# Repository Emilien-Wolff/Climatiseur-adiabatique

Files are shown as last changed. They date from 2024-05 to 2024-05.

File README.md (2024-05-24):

# Climatiseur adiabatique 🌊

> [!NOTE]
> Un projet réalisé dans le but de créer un climatiseur basé sur un principe simple : lorsque l'eau s'évapore, elle absorbe la chaleur environnante, et refroidit donc l'air

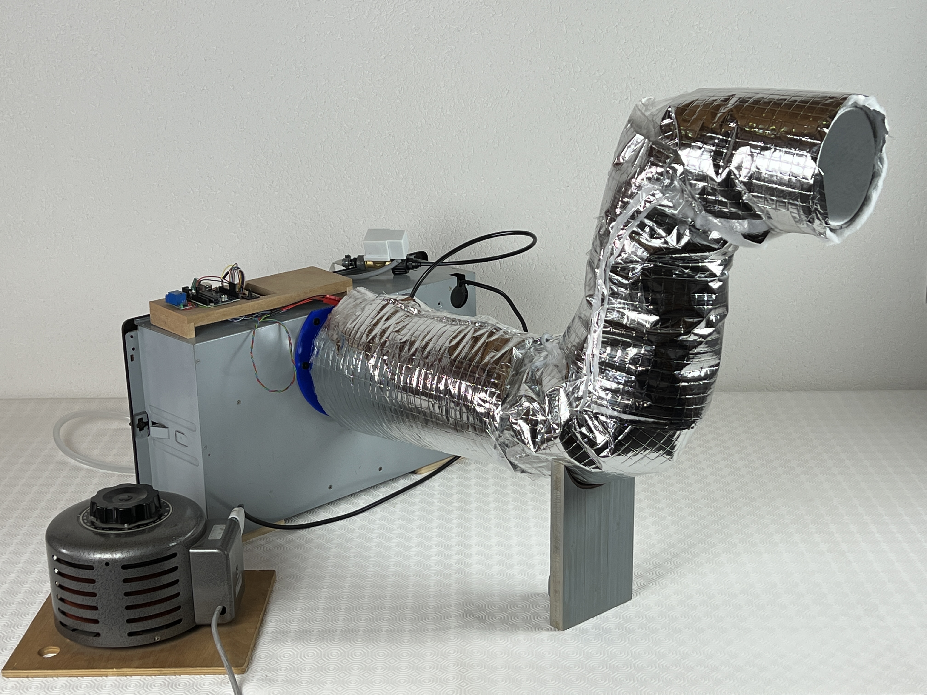
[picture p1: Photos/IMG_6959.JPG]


## Mon objectif

> Quantifier l'efficacité d'un tel système et proposer un système peu cher, compact et suffisament efficace pour permettre en été caniculaire de dormir correctement, sans travail mécanique $W_\text{méca}$ apporté (compresseur).

## Mon cahier des charges

 - Confort d'habitation en été
 - Disposer d'un système compact
 - Consommation faible d'eau et d'électricité
 - Bruit de fonctionnnement faible

## FAQ

#### Pourquoi ne pas prendre une clim classique ?

Les gaz utilisées dans les pompes à chaleur sont nocifs pour la planète, et le coût global de l'appareil est élevé pour des ménages à faibles revenus, qui de ce fait ne peuvent pas bénéficier d'une qualité de vie lors des étés chauds.

#### Risques de moisissures par l'humidité ?

Oui, j'y ai pensé, et propose des solutions à la fin de ma présentation

#### Y-a-t-il un produit final ?

Pour l'instant, non, j'ai effectué une maquette complète qui montre qu'on peut gagner environ 10°C, mais la surface d'échange devrait augmenter pour atteindre une puissance suffisante et refroidir un appartement. Projet en suspend ... Ca nécessiterait un travail sur la surface d'échange.

## 🚀 Qui suis-je ?
Je suis actuellement en deuxième année de classe préparatoire aux écoles d'ingénieur au lycée Kléber de Strasbourg

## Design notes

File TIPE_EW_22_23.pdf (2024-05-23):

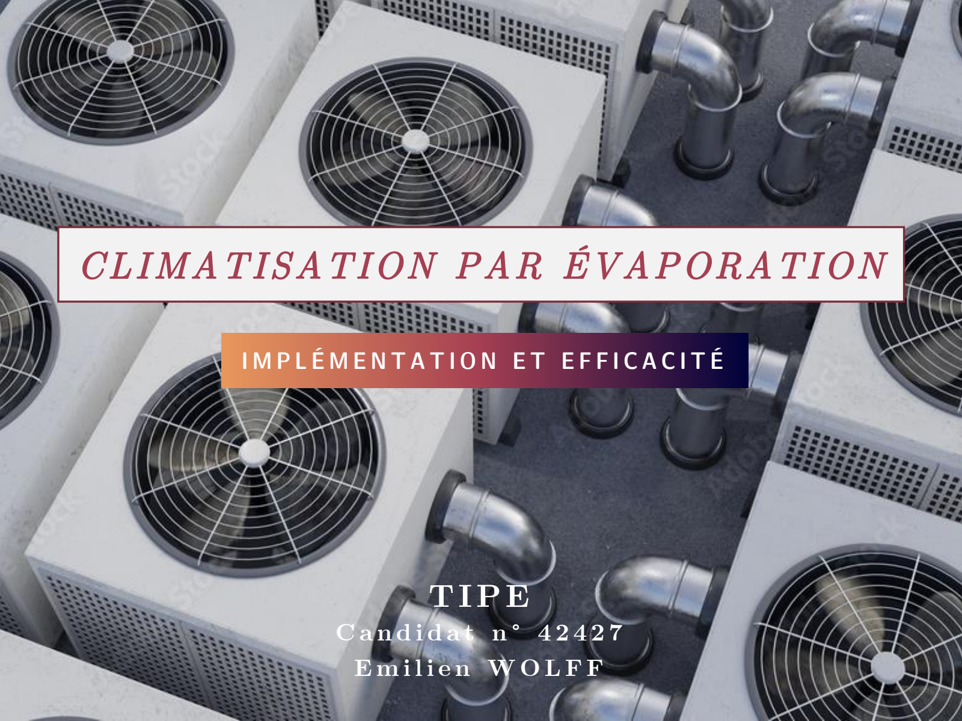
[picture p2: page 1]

# CL IMATISATION PAR ÉVAPORATION

# C a n d i d a t n ° 4 2 4 2 7

# I M P L É M E N T A T I O N E T E F F I C A C I T É

# T IPE

# E m i l i e n W O L F F

# SOMMAIRE

# 1 – Mi se e n c o nte x te e t C DC F

# 2 – Maq ue tte c o nc e ptue l l e

# 3 – Ré sul tats e t anal y se s

# 4 – C o nc l usi o n

P r o b l é m a t i q u e | : | p a r | q u e l s

# m o y e n s p e u t - on d i s p o s e r d ’ u n

s y s t è m e | de | c l i m a t i s a t i o n

# e f f i c a c e d ’ u n e p i è c e , c o m p a c t

# et p e u c o u t e u x ?

# 1 – MISE EN CONTEXTE ET CDCF

# H I S T O R I Q U E

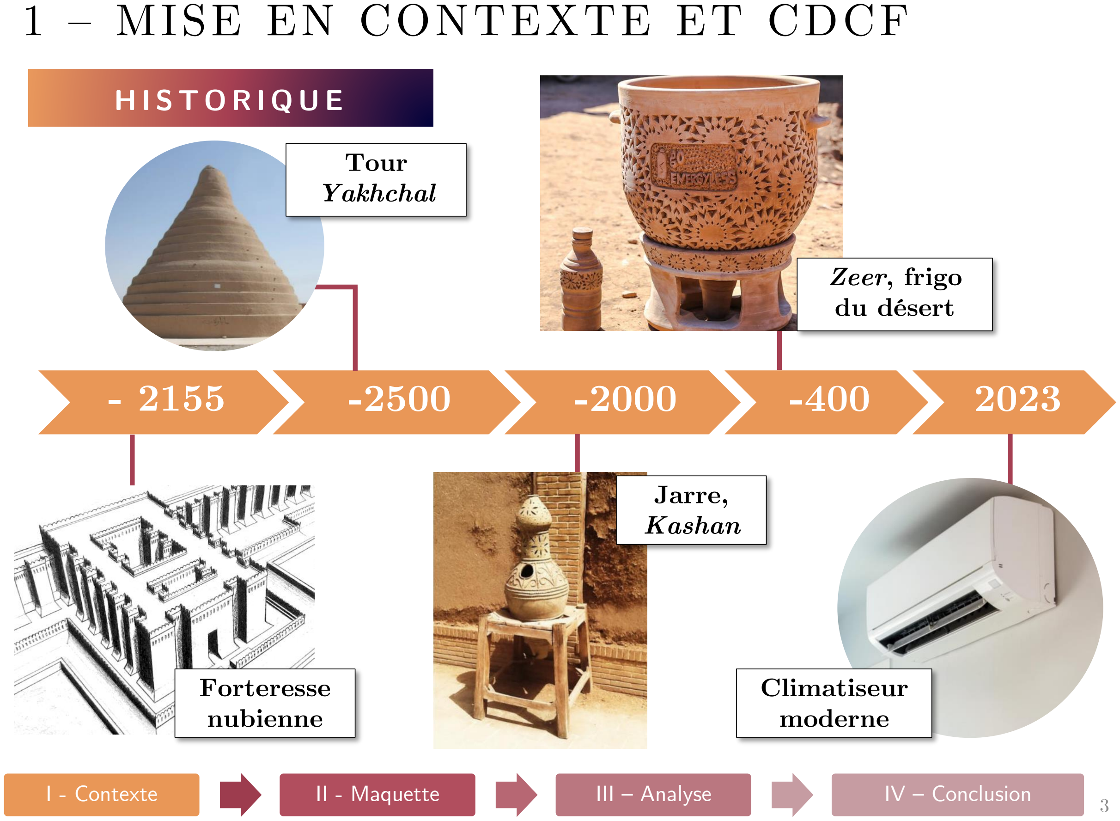
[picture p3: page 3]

- 2155 | -2500 | -2000 | -400 | 2023
I - Contexte | II - Maquette | III – Analyse | IV – Conclusion

# Forteresse nubienne

Jarre,

# Kashan

# Zeer, frigo du désert

# Climatiseur moderne

# Tour Yakhchal

# 1 – MISE EN CONTEXTE ET CDCF

# E X E M P L E

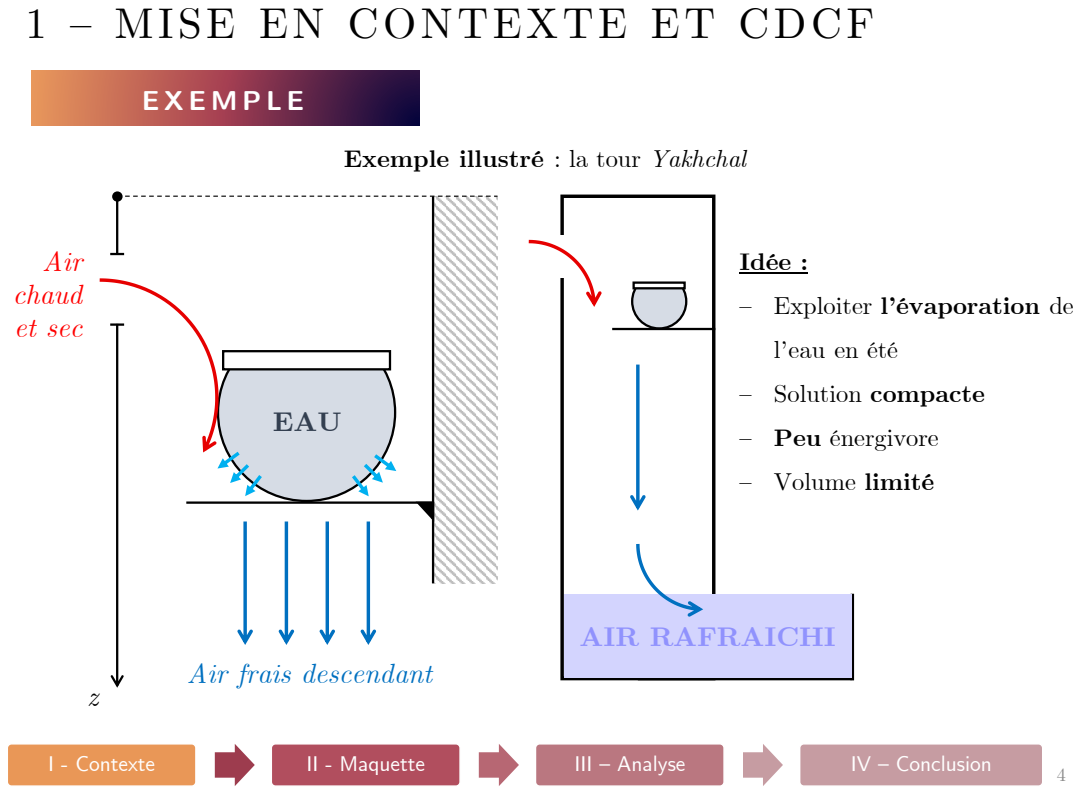
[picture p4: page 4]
Air chaud et sec; EAU; AIR RAFRAICHI

Exemple illustré : la tour Yakhchal

Idée :
– Exploiter l’évaporation de
l’eau en été
– Solution compacte
– Peu énergivore
– Volume limité

Air frais descendant

# 1 – MISE EN CONTEXTE ET CDCF

# P R I N C I P E S

18°C
20%

25°C
30%

35°C
30%

40°C
30%

## Pièce

## EXTERIEUR

# Figure 1 : Refroidissement par échangeur

28°C
30%

# – Cyclage interne de l’air

# – Compresseur, échangeurs, fluide

# – Assèchement de l’air interne

## Flux de chaleur entrant

# 1 – MISE EN CONTEXTE ET CDCF

# P R I N C I P E S

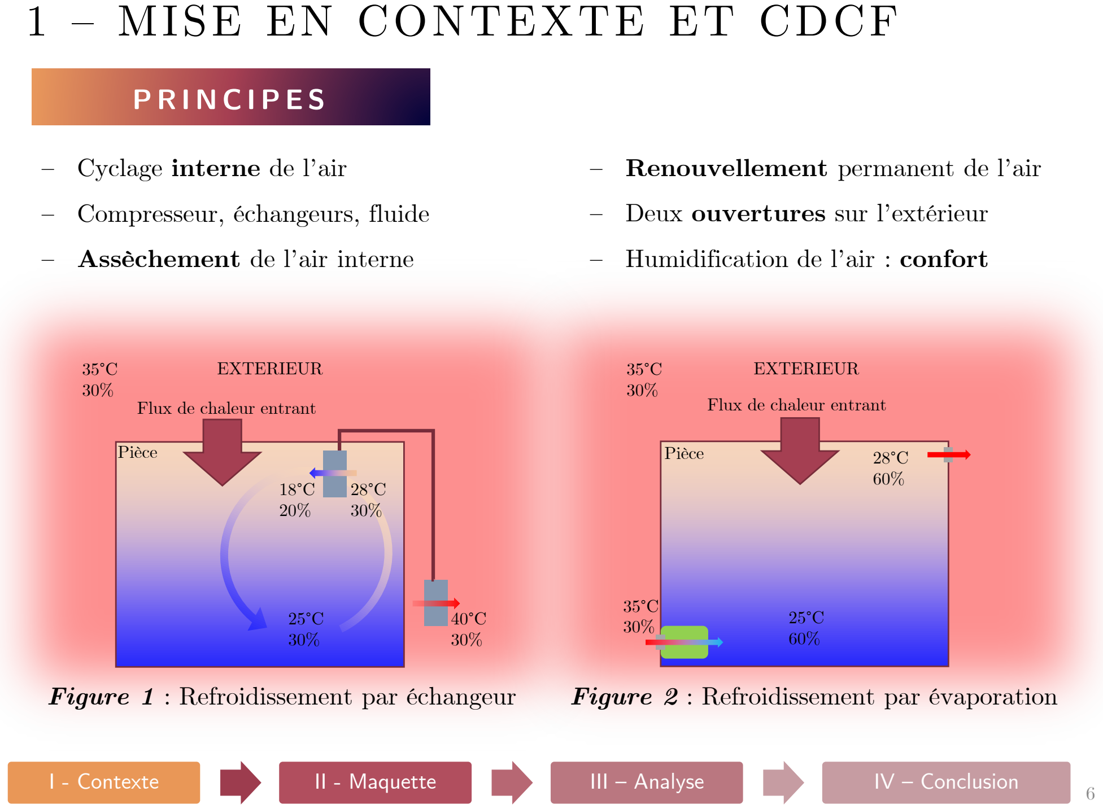
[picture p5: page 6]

# Figure 2 : Refroidissement par évaporation

# – Renouvellement permanent de l’air

# – Deux ouvertures sur l’extérieur

# – Humidification de l’air : confort

28°C
60%

25°C
60%

35°C
30%

## Pièce

## EXTERIEUR

## Flux de chaleur entrant

35°C
30%

18°C
20%

25°C
30%

35°C
30%

40°C
30%

## Pièce

## EXTERIEUR

# Figure 1 : Refroidissement par échangeur

28°C
30%

# – Cyclage interne de l’air

# – Compresseur, échangeurs, fluide

# – Assèchement de l’air interne

## Flux de chaleur entrant

# 1 – MISE EN CONTEXTE ET CDCF

# C D C F

Id | Exigence | Critère | Niveau
1 | Confort d’habitation en été | Surface de pièce | [15 m² ; 20 m² ]
| | Régulation de la température intérieure | < 25°C
| | Degré hygrométrique NF35-102 | HR% ∈ [50 ; 70]
| | Précision : erreur statique | ± 1°C
2 | Disposer d’un système compact | Taille du boitier | 300(L) × 300(l) × 1000(h)
| | Poids du dispositif | < 10 kg
3 | Consommation faible | Eau | < 20 L/jour
| | Electricité | < 50W
4 | Bruit de fonctionnement | Niveau sonore à 1m | < 42dBSPL

# 2 – MAQUETTE CONCEPTUELLE

# P R E S E N T A T I O N

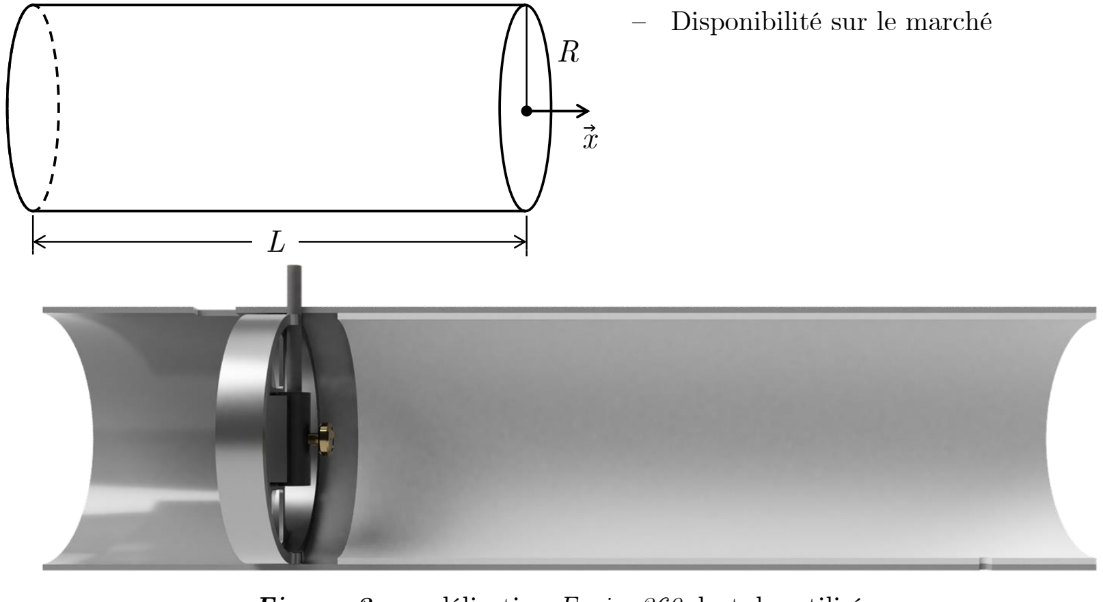
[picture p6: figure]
– Disponibilité sur le marché

# Figure 3 : modélisation Fusion360 du tube utilisé

# – Pertes de charge faibles

– Surface | d’échange | importante

# (périmètre)

# 2 – MAQUETTE CONCEPTUELLE

# P R E S E N T A T I O N

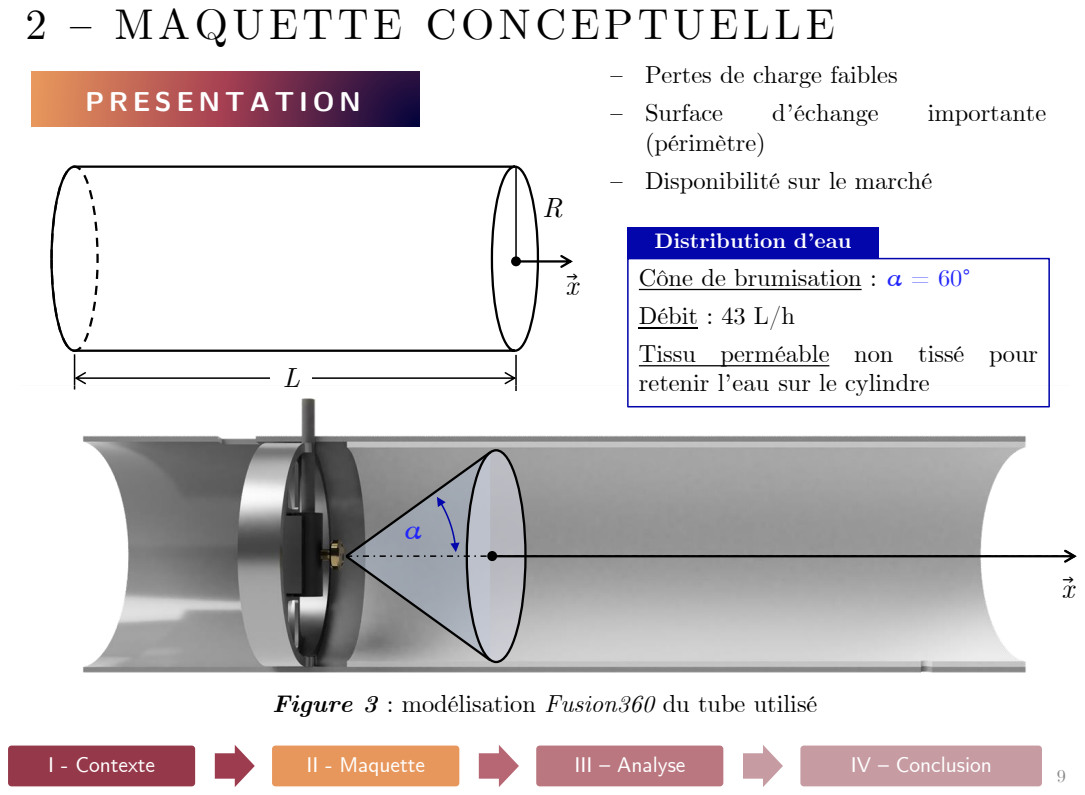
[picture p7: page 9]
– Surface; d’échange; importante

– Pertes de charge faibles
(périmètre)
– Disponibilité sur le marché

Distribution d’eau
Cône de brumisation : α = 60°
Débit : 43 L/h
Tissu perméable non tissé pour
retenir l’eau sur le cylindre

Figure 3 : modélisation Fusion360 du tube utilisé

# 2 – MAQUETTE CONCEPTUELLE

# P R E S E N T A T I O N

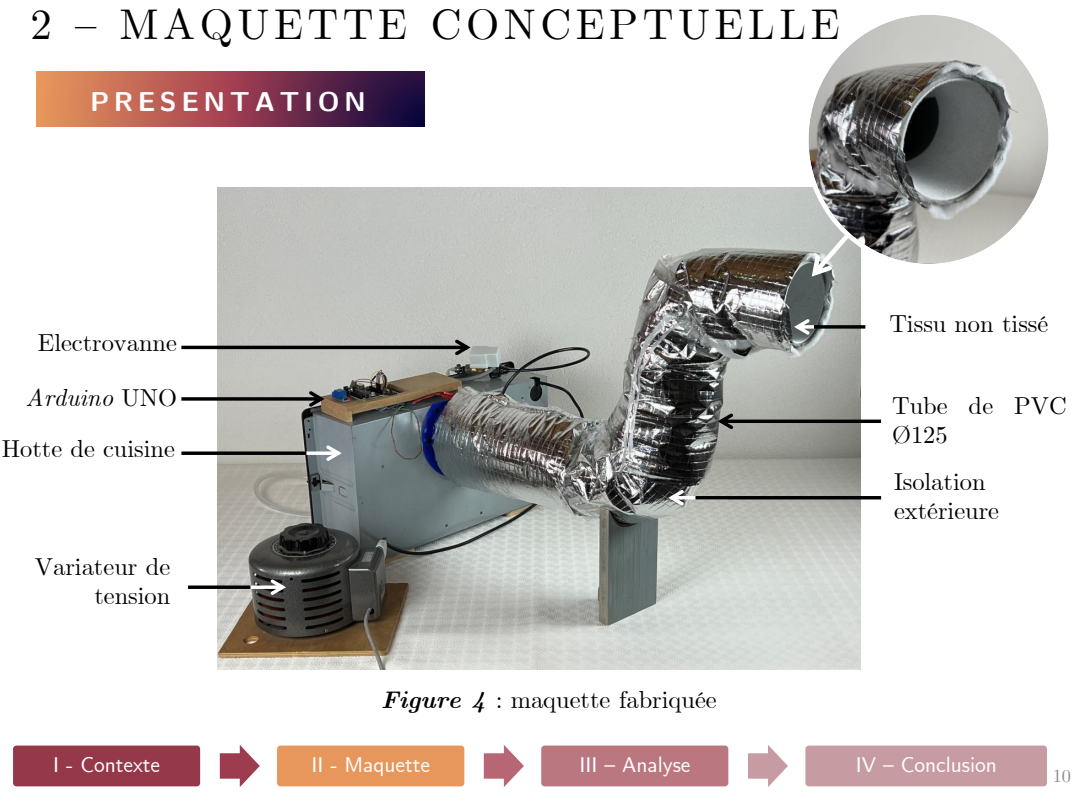
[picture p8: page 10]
Isolation extérieure; Arduino UNO; Variateur de tension; Electrovanne; Tube de PVC Ø125

Tissu non tissé

Hotte de cuisine

Figure 4 : maquette fabriquée

# 2 – MAQUETTE CONCEPTUELLE

# P R E S E N T A T I O N

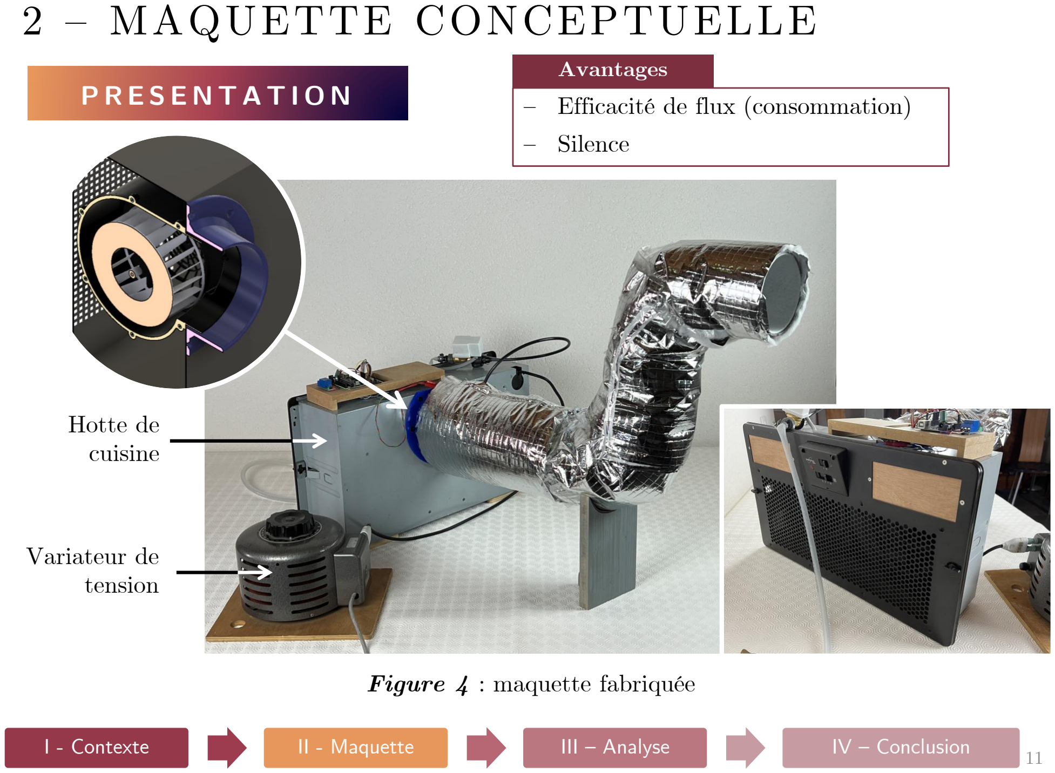
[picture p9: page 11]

# Hotte de cuisine

# Figure 4 : maquette fabriquée

# Variateur de tension

# – Efficacité de flux (consommation) – Silence

# Avantages

# 2 – MAQUETTE CONCEPTUELLE

# E T A L O N N A G E

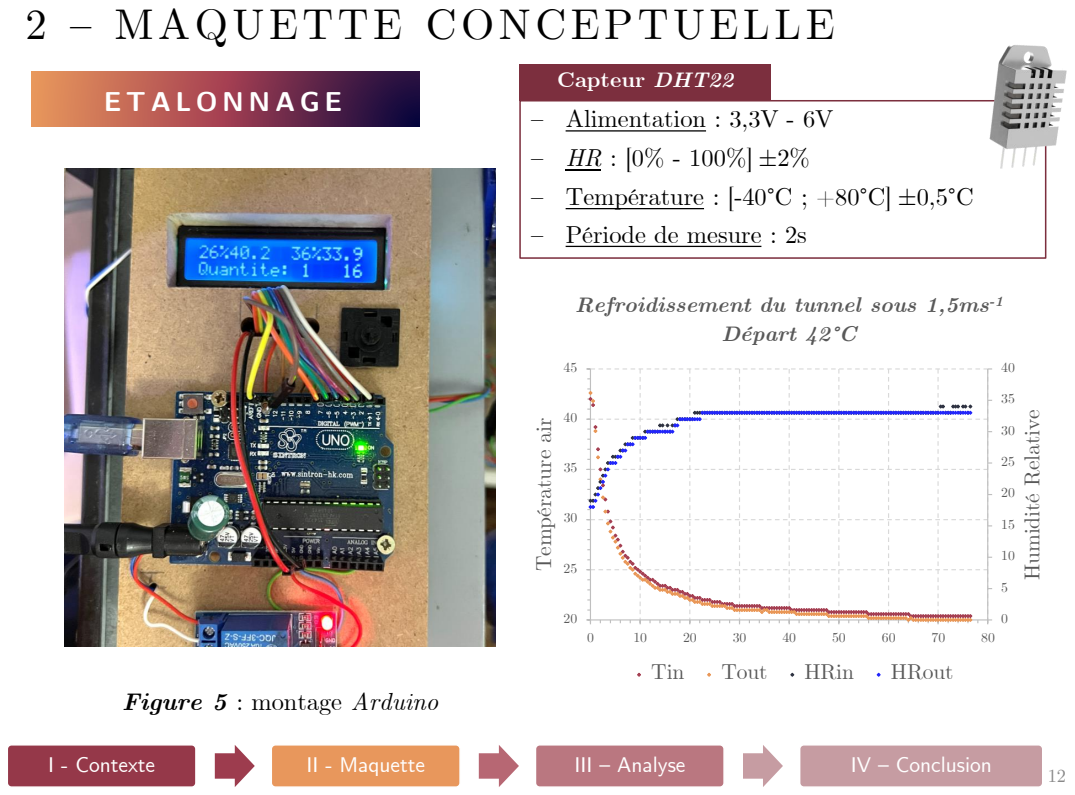
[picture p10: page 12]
– Alimentation : 3,3V - 6V; – Température : [-40°C ; +80°C] ±0,5°C; – Période de mesure : 2s; Capteur DHT22; Humidité Relative; Température air; Départ 42°C; Tin; Tout; HRin; HRout

Refroidissement du tunnel sous 1,5ms⁻¹

Figure 5 : montage Arduino

# 2 – MAQUETTE CONCEPTUELLE

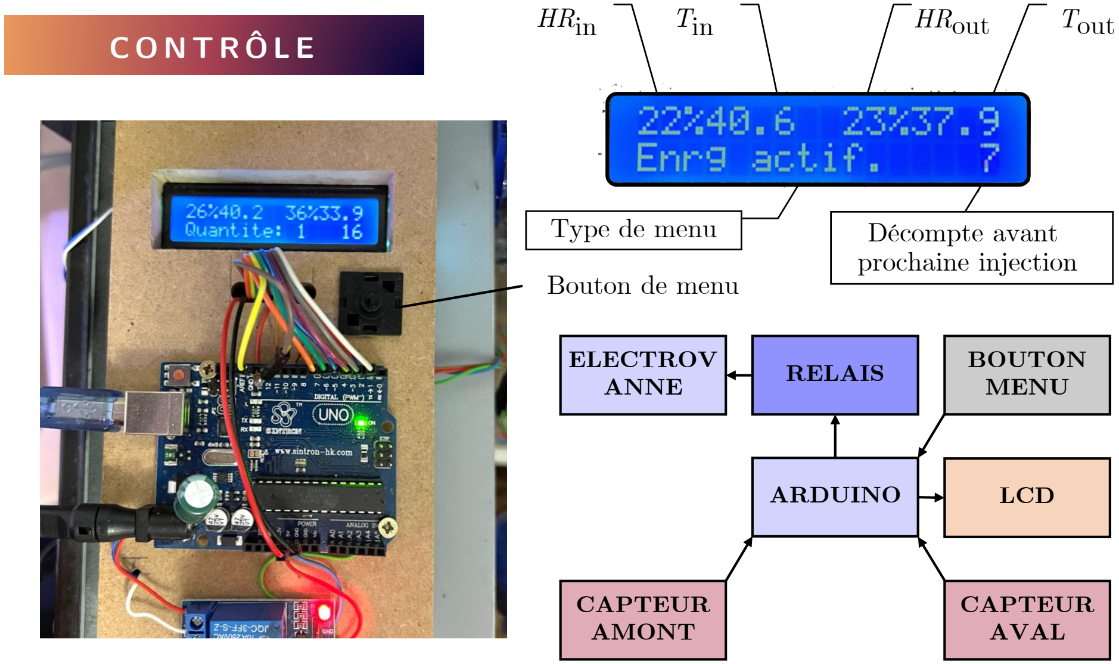
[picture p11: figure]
CAPTEUR AMONT; BOUTON MENU; LCD; RELAIS; ARDUINO; ELECTROV ANNE; CAPTEUR AVAL; Bouton de menu; Type de menu; HRin; Tin; HRout; Tout; Décompte avant prochaine injection

# Figure 5 : montage Arduino

# Figure 6 : schéma bloc global

# 2 – MAQUETTE CONCEPTUELLE

# S T R U C T U R E P R O G R A M M E

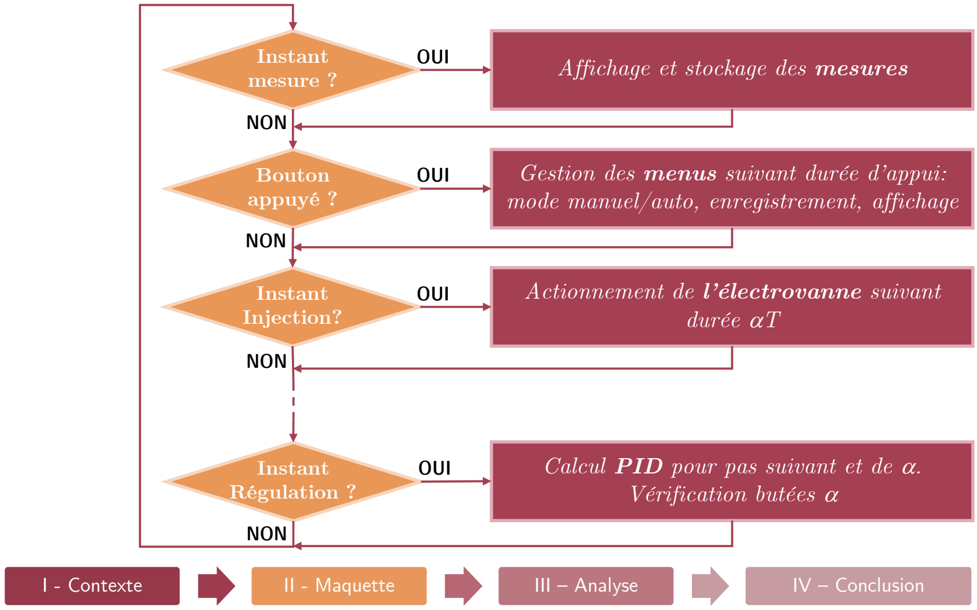
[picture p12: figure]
Instant mesure ?; Bouton appuyé ?; Instant Injection?; Instant Régulation ?; Affichage et stockage des mesures; Actionnement de l’électrovanne suivant durée αT; Calcul PID pour pas suivant et de α. Vérification butées α; OUI; NON

# Gestion des menus suivant durée d’appui: mode manuel/auto, enregistrement, affichage

# Figure 7 : organigramme de programmation

# 2 – MAQUETTE CONCEPTUELLE

# M E S U R E D U T A U

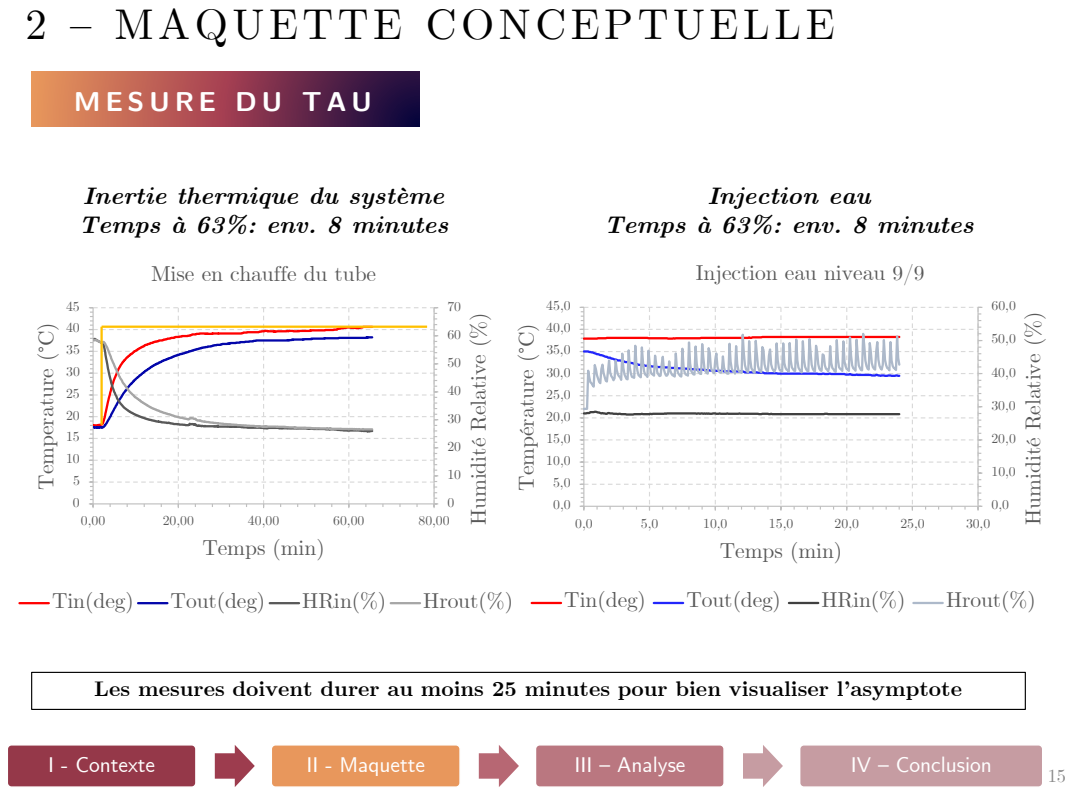
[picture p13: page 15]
Injection eau; Humidité Relative (%); Temperature (°C); Temps (min); Tin(deg); Tout(deg); HRin(%); Hrout(%); Température (°C)

Inertie thermique du système
Temps à 63%: env. 8 minutes

Mise en chauffe du tube

Injection eau niveau 9/9

Les mesures doivent durer au moins 25 minutes pour bien visualiser l’asymptote

# 2 – MAQUETTE CONCEPTUELLE

# T H E O R I E

# - Objectif initial: Etablir une relation entre la densité de flux de molécules

d’eau et la chute de température de l’air à l’interface.

# Phénomène d’évaporation étudié depuis 150 ans et pas encore totalement compris

‒ | Hertz, | 1882
‒ | Stefan, | 1889
‒ | Knudsen, 1915
‒ | Kennard, 1938
‒ | Knacke, | 1956

# 2 – MAQUETTE CONCEPTUELLE

# T H E O R I E

# - Objectif initial: Etablir une relation entre la densité de flux de molécules

d’eau et la chute de température de l’air à l’interface.

# Phénomène d’évaporation étudié depuis 150 ans et pas encore totalement compris

‒ | Hertz, | 1882
‒ | Stefan, | 1889
‒ | Knudsen, 1915
‒ | Kennard, 1938
‒ | Knacke, | 1956
‒ | Wolff | 2023 …
- Stratégie: Intuitivement, les grandeurs suivantes sont reliées.

# ‒ ΔT(Dmeau

# , Dmair) (1) ‒ Dmeau

(Ppart eau) | (2)

# De plus, certaines grandeurs dépendent de la température, qui varie le long

du tube. Complexité.

# 2 – MAQUETTE CONCEPTUELLE

# T H E O R I E

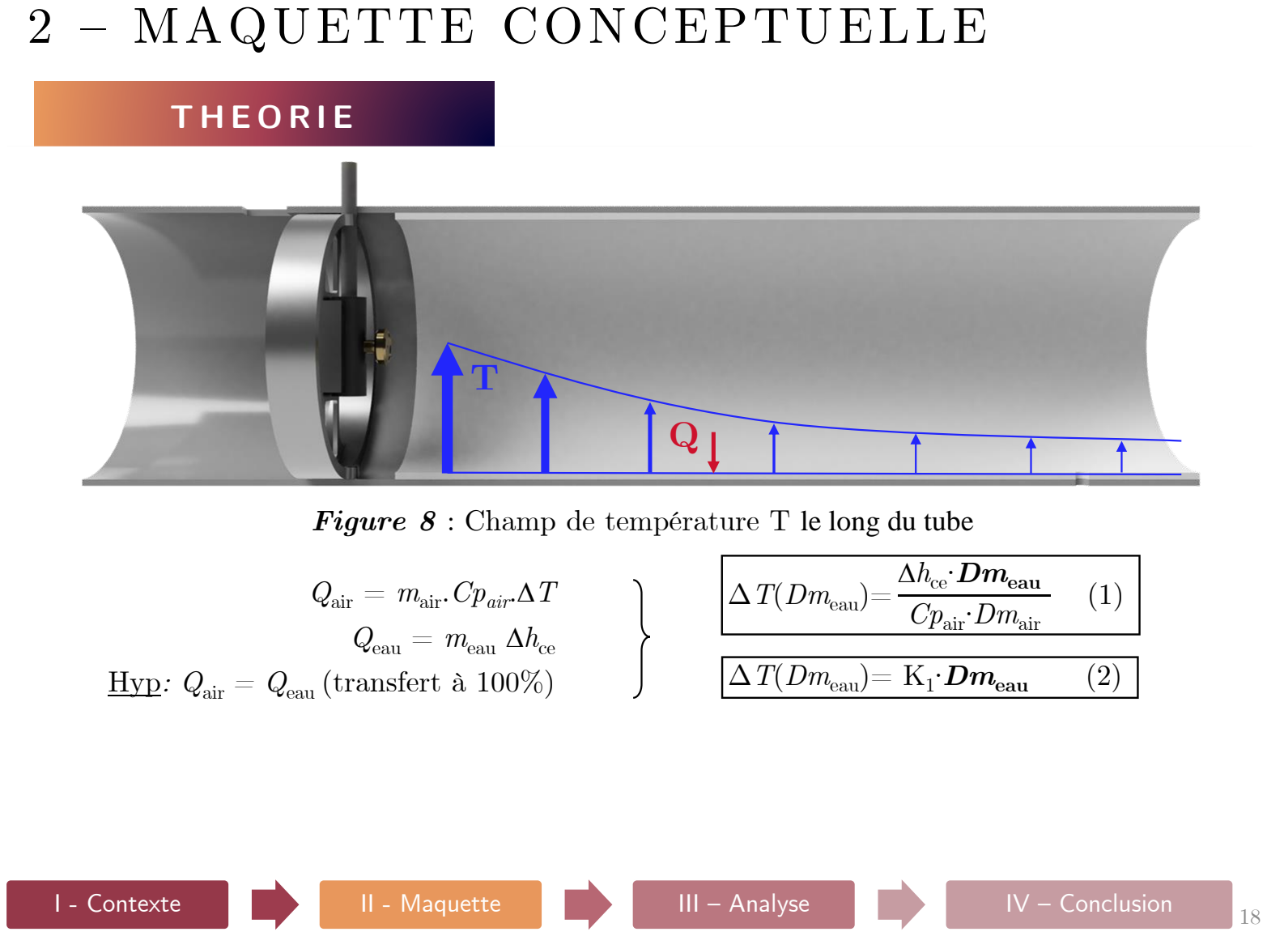
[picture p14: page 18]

## Qair = mair.Cpair.ΔT

## Qeau = meau Δhce

# Hyp: Qair = Qeau (transfert à 100%)

# Figure 8 : Champ de température T le long du tube

T
Q

# ΔT(Dmeau)= Δhce∙Dmeau

## Cpair∙Dmair

(1)

# ΔT(Dmeau)= K1

# ∙Dmeau (2)

# 2 – MAQUETTE CONCEPTUELLE

# T H E O R I E

## Qair = mair.Cpair.ΔT

## Qeau = meau Δhce

# Hyp: Qair = Qeau (transfert à 100%)

# Figure 8 : Champ de température T le long du tube

T
Q

# Valable tant que Dmeau reste en dessous du maximum possible d’évaporation ( Dmeau(T) )max

Q’=0

# ΔT(Dmeau)= Δhce∙Dmeau

## Cpair∙Dmair

(1)

# ΔT(Dmeau)= K1

# ∙Dmeau (2)

# 2 – MAQUETTE CONCEPTUELLE

# T H E O R I E

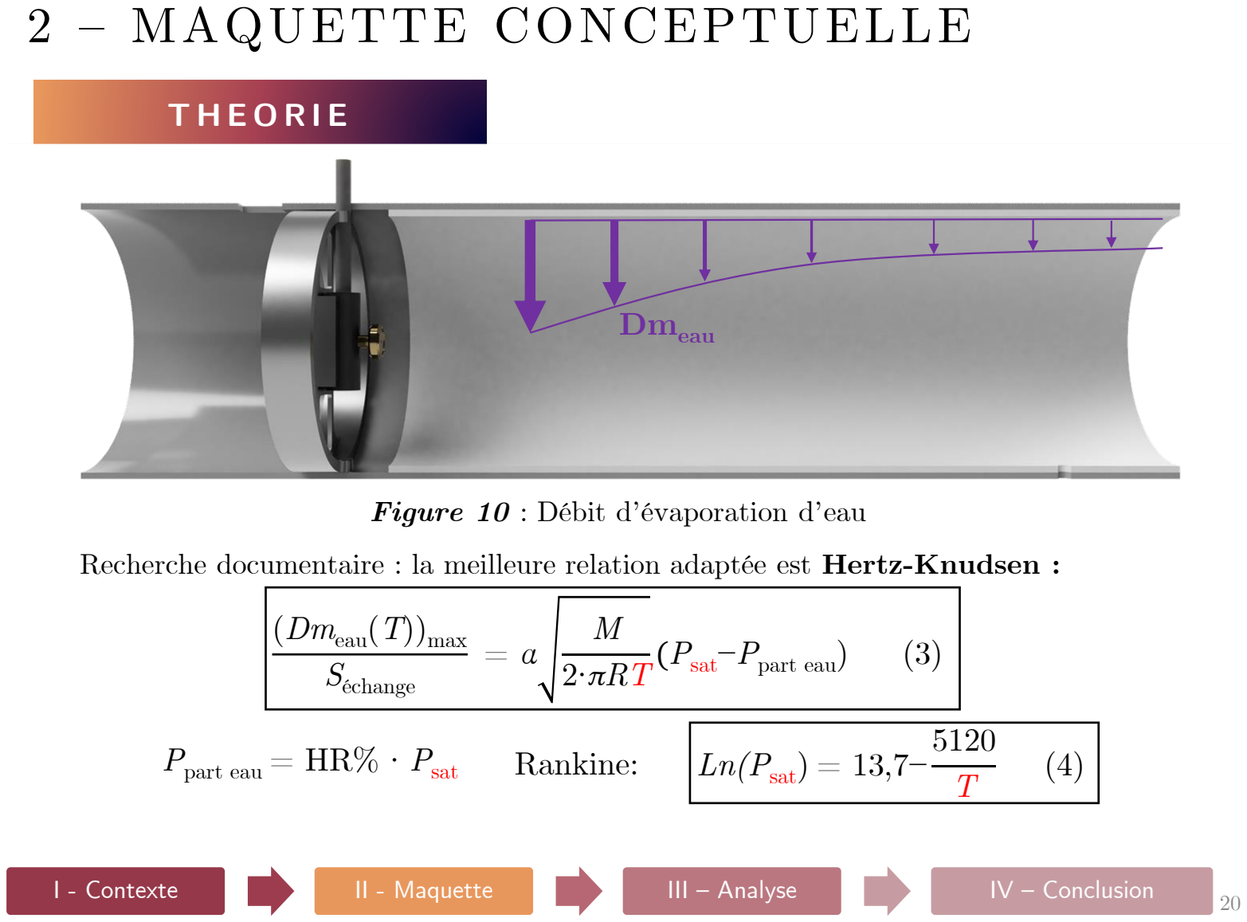
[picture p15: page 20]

# Figure 10 : Débit d’évaporation d’eau

# Recherche documentaire : la meilleure relation adaptée est Hertz-Knudsen :

# Ppart eau = HR% ∙ Psat Rankine:

# Dmeau

# (Dmeau(T))max

# Séchange

= α

M

# 2∙πRT

# (Psat−Ppart eau) (3)

# Ln(Psat) = 13,7−

5120
T

(4)

# 2 – MAQUETTE CONCEPTUELLE

# T H E O R I E

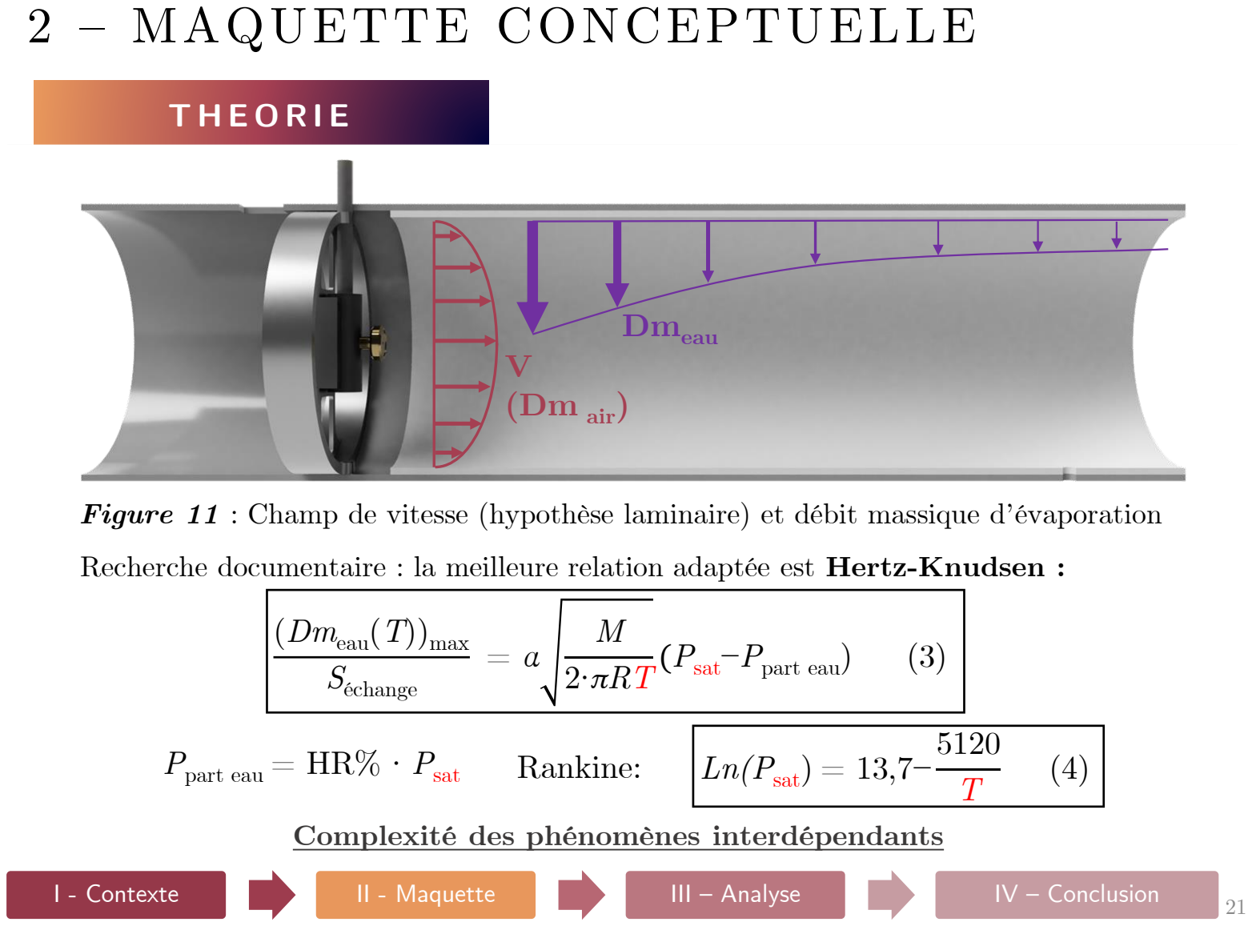
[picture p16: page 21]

V

# (Dm air)

# Figure 11 : Champ de vitesse (hypothèse laminaire) et débit massique d’évaporation

# Recherche documentaire : la meilleure relation adaptée est Hertz-Knudsen :

Complexité des phénomènes interdépendants (https://www.google.com/url?rct=j&q=&esrc=s&cd=&cad=rja&uact=8)

# Dmeau

# Ppart eau = HR% ∙ Psat Rankine:

# (Dmeau(T))max

# Séchange

= α

M

# 2∙πRT

# (Psat−Ppart eau) (3)

# Ln(Psat) = 13,7−

5120
T

(4)

# 2 – MAQUETTE CONCEPTUELLE

# F C T D E T R A N S F E R T

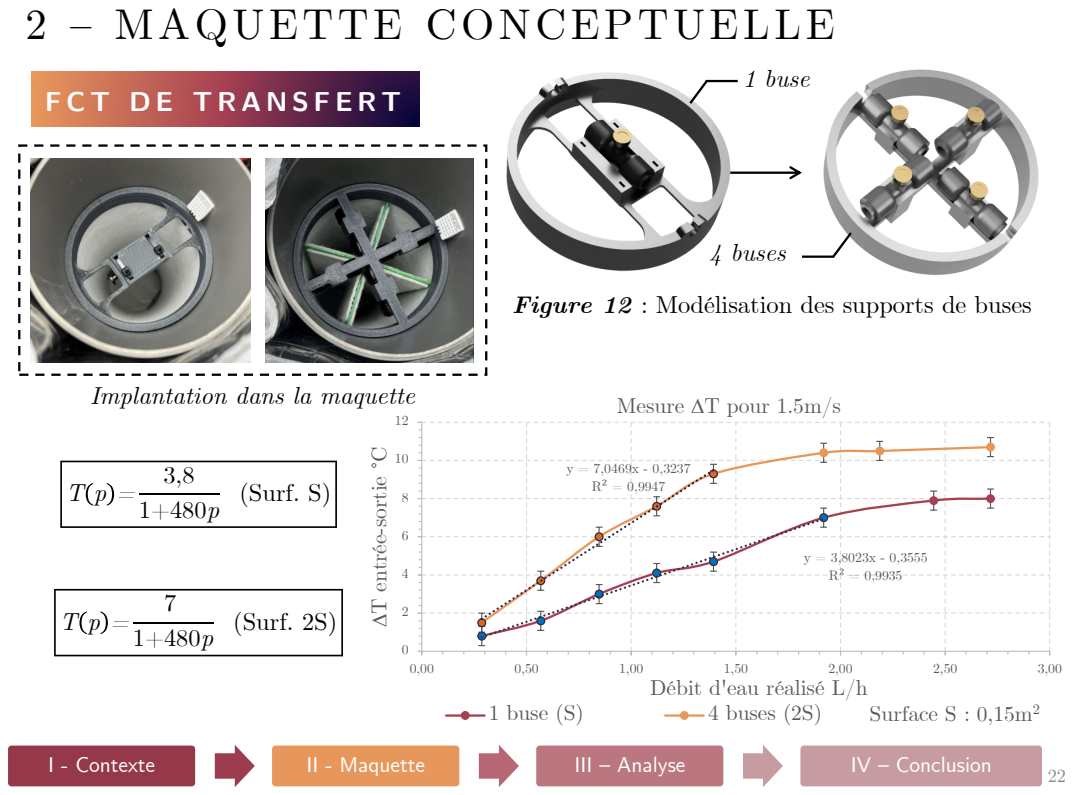
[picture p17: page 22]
1 buse (S); 4 buses (2S); (Surf. S); 1 buse; 4 buses; (Surf. 2S); Surface S : 0,15m²

Figure 12 : Modélisation des supports de buses

Implantation dans la maquette

Mesure ΔT pour 1.5m/s

ΔT entrée-sortie °C

Débit d'eau réalisé L/h

# A D E Q U A T I O N A U B E S O I N ?

# 3 – RÉSULTATS ET ANALYSES

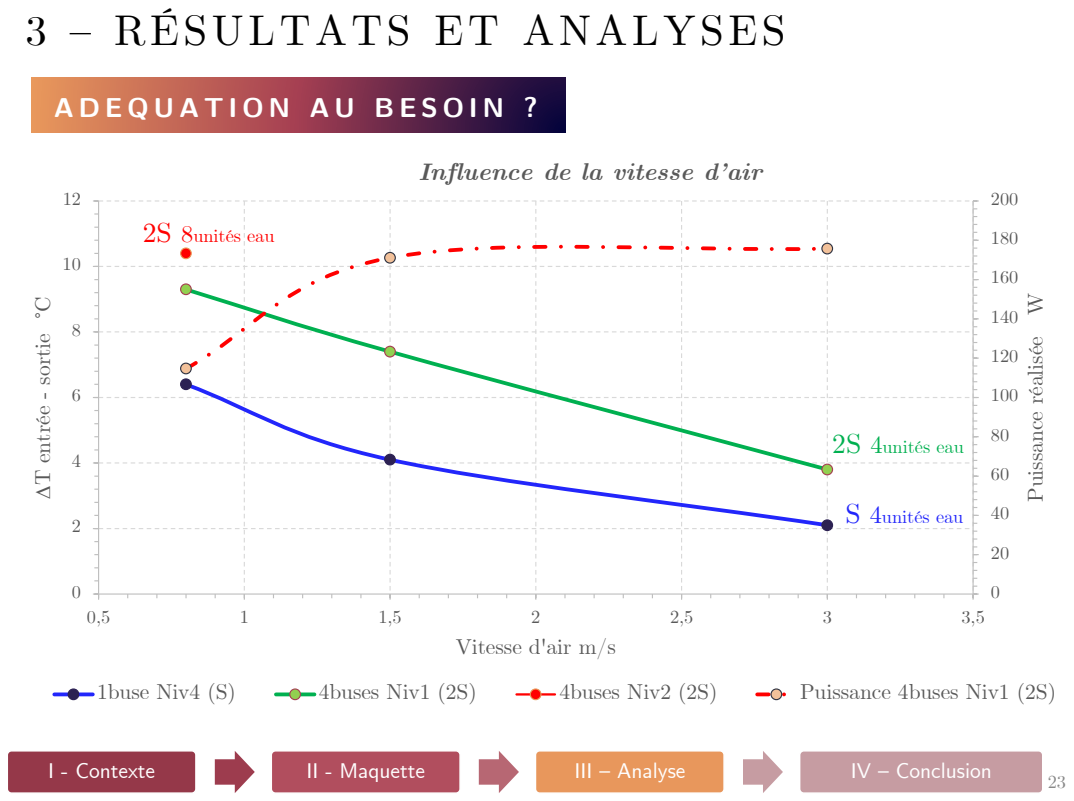
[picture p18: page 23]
Puissance réalisée W; T entrée - sortie °C; Vitesse d'air m/s; 1buse Niv4 (S); 4buses Niv1 (2S); 4buses Niv2 (2S); Puissance 4buses Niv1 (2S); 2S 8unités; eau

Influence de la vitesse d’air

2S 4unités eau

S 4unités eau

160

180

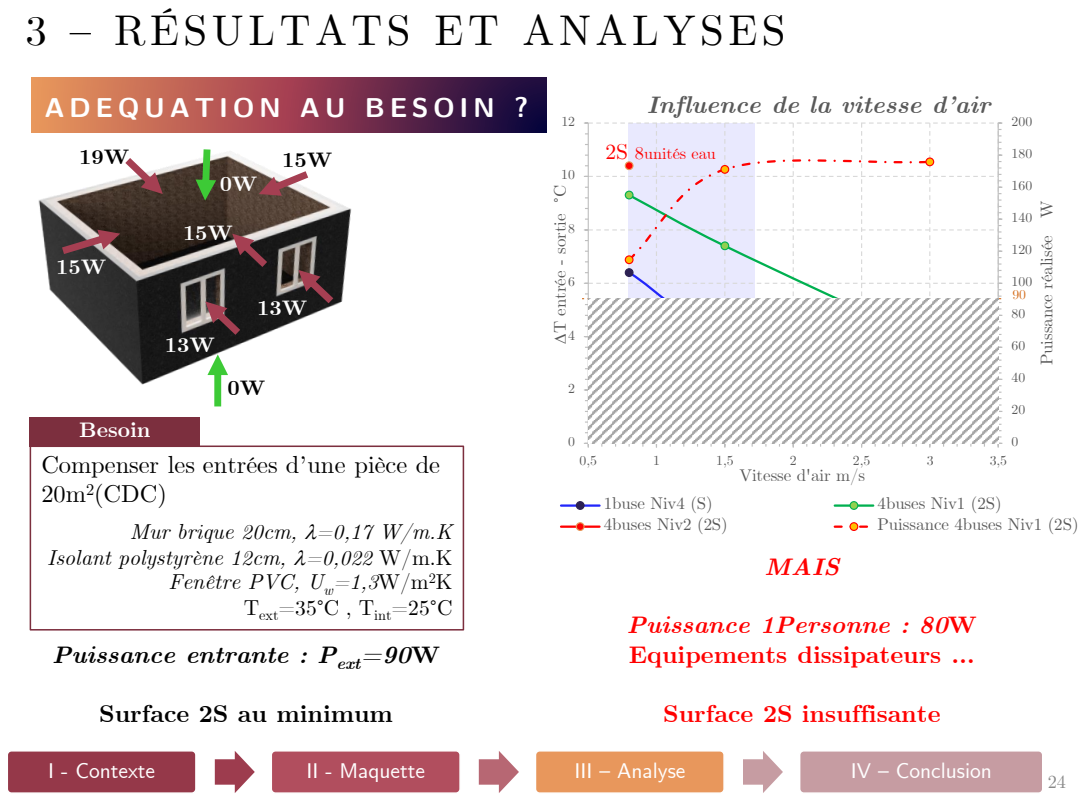
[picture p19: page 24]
Puissance réalisée W; Vitesse d'air m/s; 1buse Niv4 (S); 4buses Niv1 (2S); 4buses Niv2 (2S); Puissance 4buses Niv1 (2S); Isolant polystyrène 12cm, λ=0,022 W/m.K; Text=35°C , Tint=25°C; 2S 8unités eau; MAIS; Puissance 1Personne : 80W Equipements dissipateurs …; Surface 2S insuffisante

3 – RÉSULTATS ET ANALYSES

Influence de la vitesse d’air

ΔT entrée - sortie °C

2S 4unités eau

S 4unités eau

Besoin
Compenser les entrées d’une pièce de
(CDC)
Mur brique 20cm, λ=0,17 W/m.K

Fenêtre PVC, Uw=1,3W/m²K

Puissance entrante : Pext=90W

Surface 2S au minimum

# 3 – RÉSULTATS ET ANALYSES

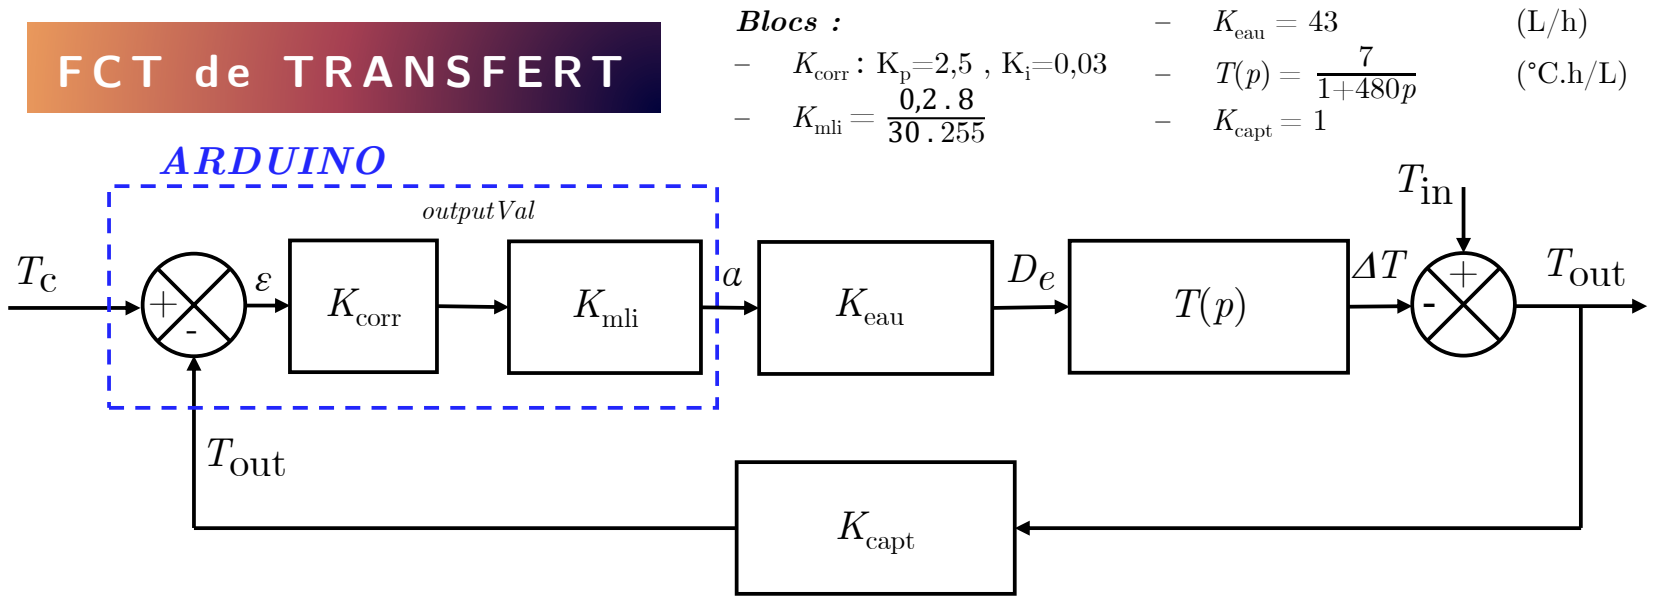
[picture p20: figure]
Kcorr; Keau; Kcapt; ARDUINO; Tout; Tin; Kmli; outputVal; Blocs :; Kcorr : Kp=2,5 , Ki=0,03; Kmli =; Keau = 43; Kcapt = 1

# Figure 13 : schéma bloc du système de régulation

# 3 – RÉSULTATS ET ANALYSES

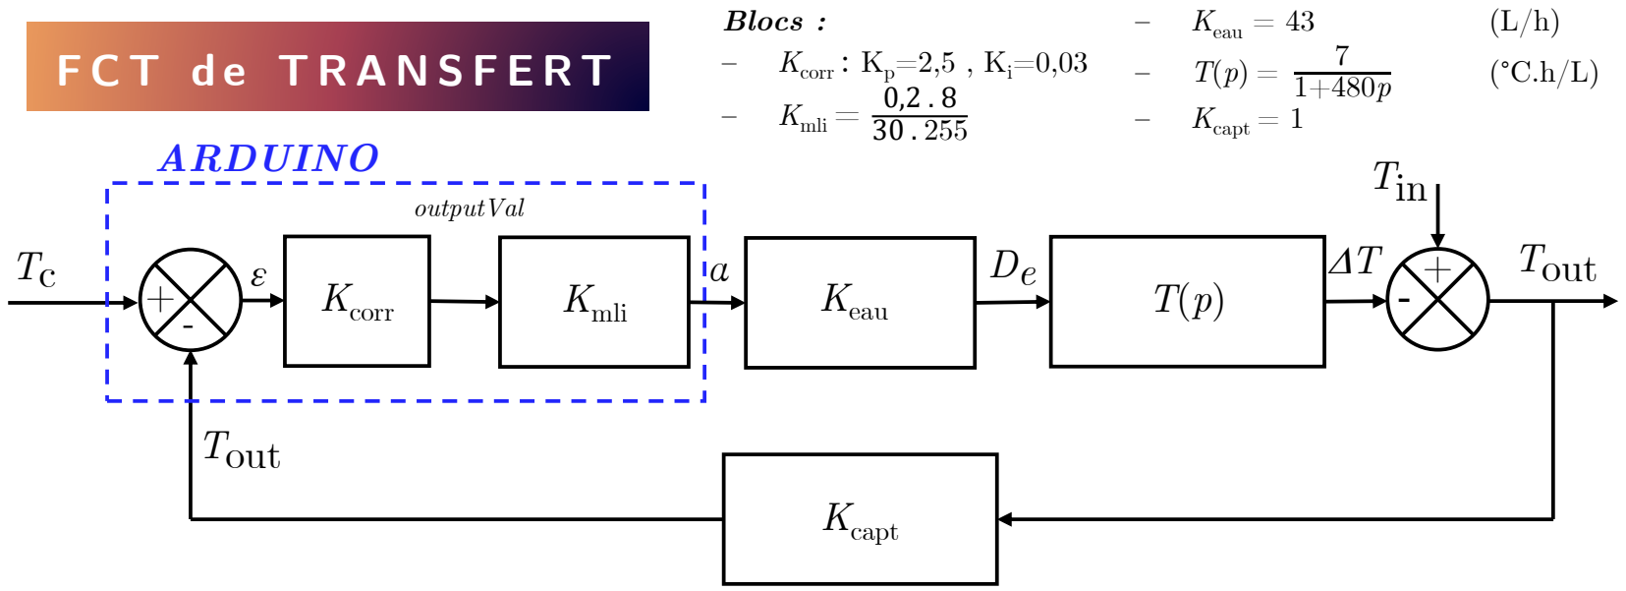
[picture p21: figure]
Kcorr; Keau; Kcapt; ARDUINO; Tout; Tin; Kmli; outputVal; Blocs :; Kcorr : Kp=2,5 , Ki=0,03; Kmli =; Keau = 43; Kcapt = 1

# Figure 13 : schéma bloc du système de régulation

Modélisation de la MLI : exemple avec une quantité de 4 unités de 0,2s chacune, 8 unités max.

## Dm buse

0

# Réponse à un échelon à 1.5m/s

# 3 – RÉSULTATS ET ANALYSES

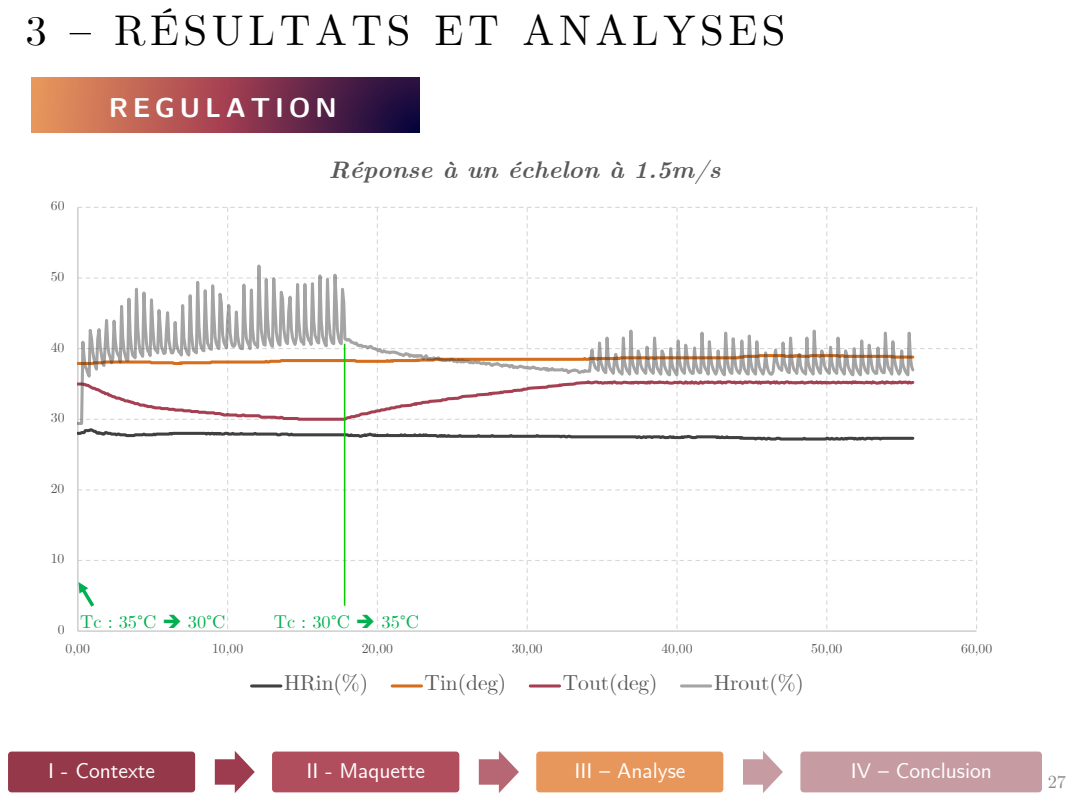
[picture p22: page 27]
HRin(%); Tin(deg); Tout(deg); Hrout(%)

# 3 – RÉSULTATS ET ANALYSES

# B I L A N E N E R G E T I Q U E

# Système

PVentil | PThermo

## PRégul

# EAU

2W

12W

≈170W

# L’énergie provient du changement de phase

de l’eau.

Le litre d’eau coute environ 0,3 cents.

# L’énergie équivalente à sa vaporisation

couterait 12,5 cents en électrique.

# Un bilan en puissance est très favorable:

# COP =

## Pthermo

## Pventil+Pregul

≈ 1200%

# Mais la puissance absolue dépend de la surface d’échange

Le COP d’une climatisation est de 500% au mieux.

# Figure 14 : Bilan de puissance de la machine

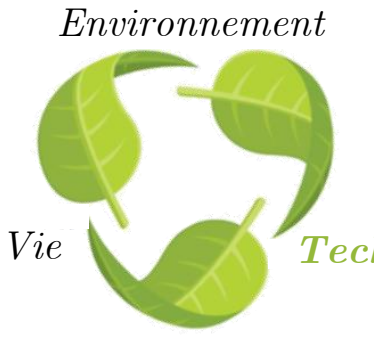
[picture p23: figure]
Environnement; Vie

# 4 – CONCLUSION

# T E C H N I Q U E

Id | Exigence | Critère | Niveau
1 | Confort d’habitation en été | Surface de pièce | 20 m²
| | Régulation de la température intérieure | < 25°C
| | Degré hygrométrique NF35-102 | HR% ∈ [50 ; 70]
| | Précision : erreur statique | ± 1°C
2 | Disposer d’un système compact | Taille du boitier | 300(L) × 300(l) × 1000(h)
| | Poids du dispositif | < 10 kg
3 | Consommation faible | Eau | < 20 L/jour
| | Electricité | < 50W
4 | Bruit de fonctionnement | Niveau sonore à 1m | < 42dBSPL

# Technique

# 4 – CONCLUSION

# T E C H N I Q U E

Id | Exigence | Critère | Niveau
1 | Confort d’habitation en été | Surface de pièce | 20 m²
| | Régulation de la température intérieure | < 25°C
| | Degré hygrométrique NF35-102 | HR% ∈ [50 ; 70]
| | Précision : erreur statique | ± 1°C
2 | Disposer d’un système compact | Taille du boitier | 300(L) × 300(l) × 1000(h)
| | Poids du dispositif | < 10 kg
3 | Consommation faible | Eau | < 20 L/jour
| | Electricité | < 50W
4 | Bruit de fonctionnement | Niveau sonore à 1m | < 42dBSPL

# Technique

# 4 – CONCLUSION

# B I L A N

# P r o b l é m a t i q u e : p a r q u e l s m o y e n s

p e u t - on | d i s p o s e r d ’ u n | s y s t è m e de

c l i m a t i s a t i o n e f f i c a c e d ’ u n e p i è c e ,

# c o m p a c t et p e u c o u t e u x ?

# ANNEXE 1 – AXES D’OPTIMISATION

Type | Nature | Solution | Illustration
| Encombrement du produit | Plusieurs tubes en parallèle
Taux d’évaporation baisse quand l’humidité augmente dans le tube | Tubes courts en parallèle
Dépôt de calcaire | Filtration à résine amont ou nettoyage périodique
Puissance du ventilateur plus adaptée et aussi silencieux | Utilisation d’un ventilateur radial plus petit
Utilisation de la fraicheur nocturne | Augmenter le débit d’air sans injection la nuit
Risque | Salmonelles | Lampe UV
Usage | Nécessité d’eau sous pression | Bac et écoulement par gravité
| Entrée et sortie d’air de la pièce | Caches adaptables à une fenêtre entr’ouverte

# Performance

# ANNEXE 2 – SIMULATIONS SC ILAB

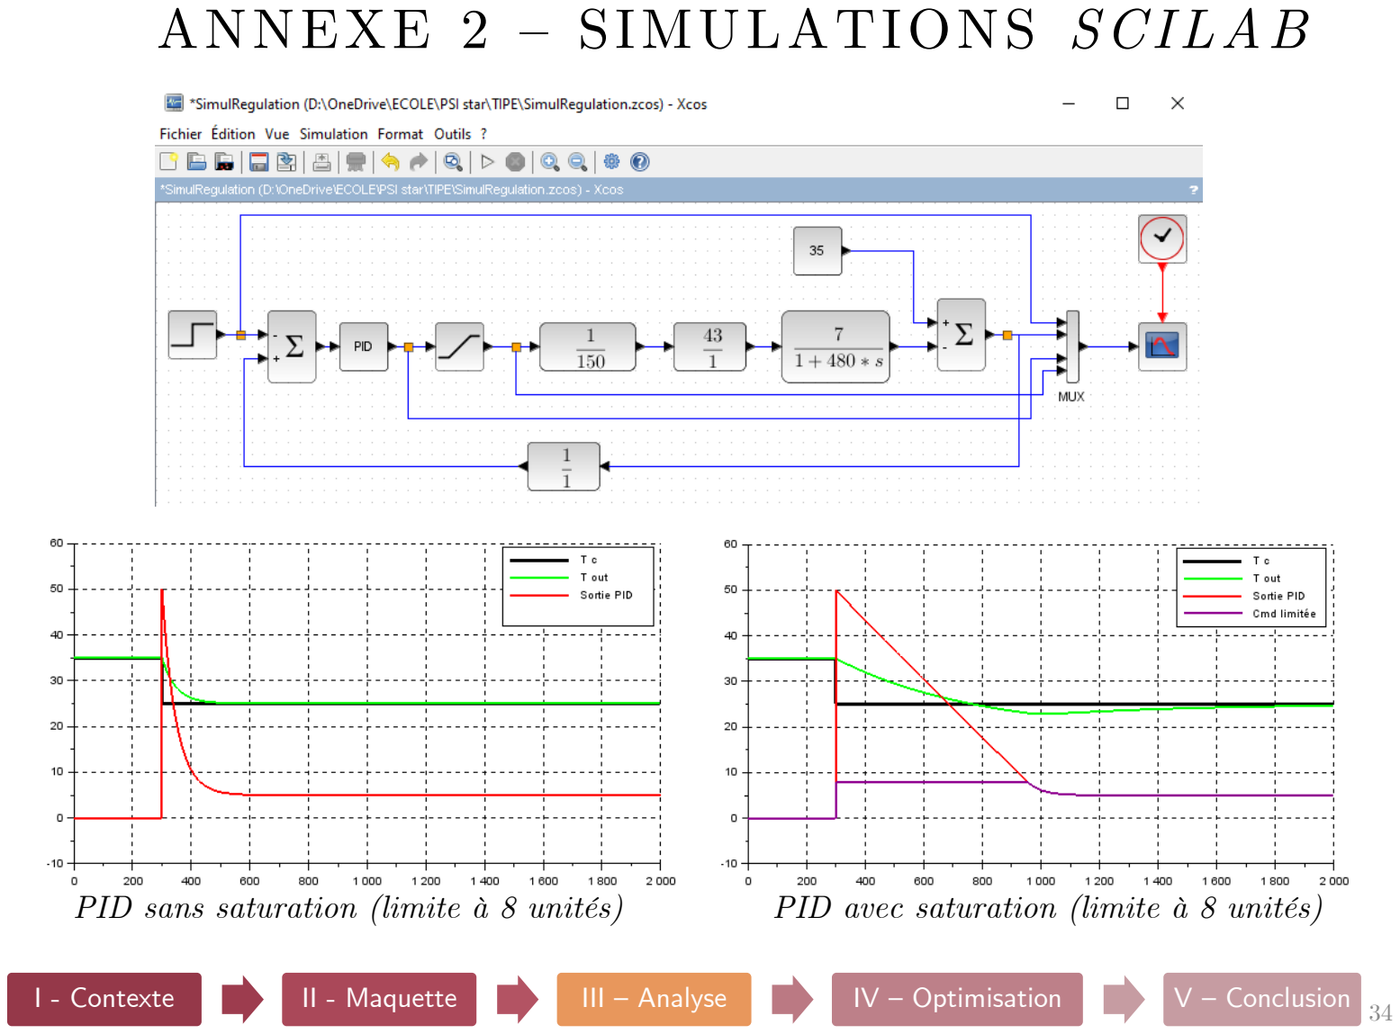
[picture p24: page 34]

34 I - Contexte | II - Maquette | III – Analyse | IV – Optimisation | V – Conclusion
PID sans saturation (limite à 8 unités) | PID avec saturation (limite à 8 unités)

# Diagramme de l’air humide

# Altitude 0m, pression 101325 Pa

# Air en entrée Air en sortie pour 2S Maximum possible

# Légende

# ANNEXE 3 – DIAGRAMME AIR HUMIDE

# Abaissement de température pas loin du maximum

# ANNEXE 4 – MODÉLISATION FUS ION 3 6 0

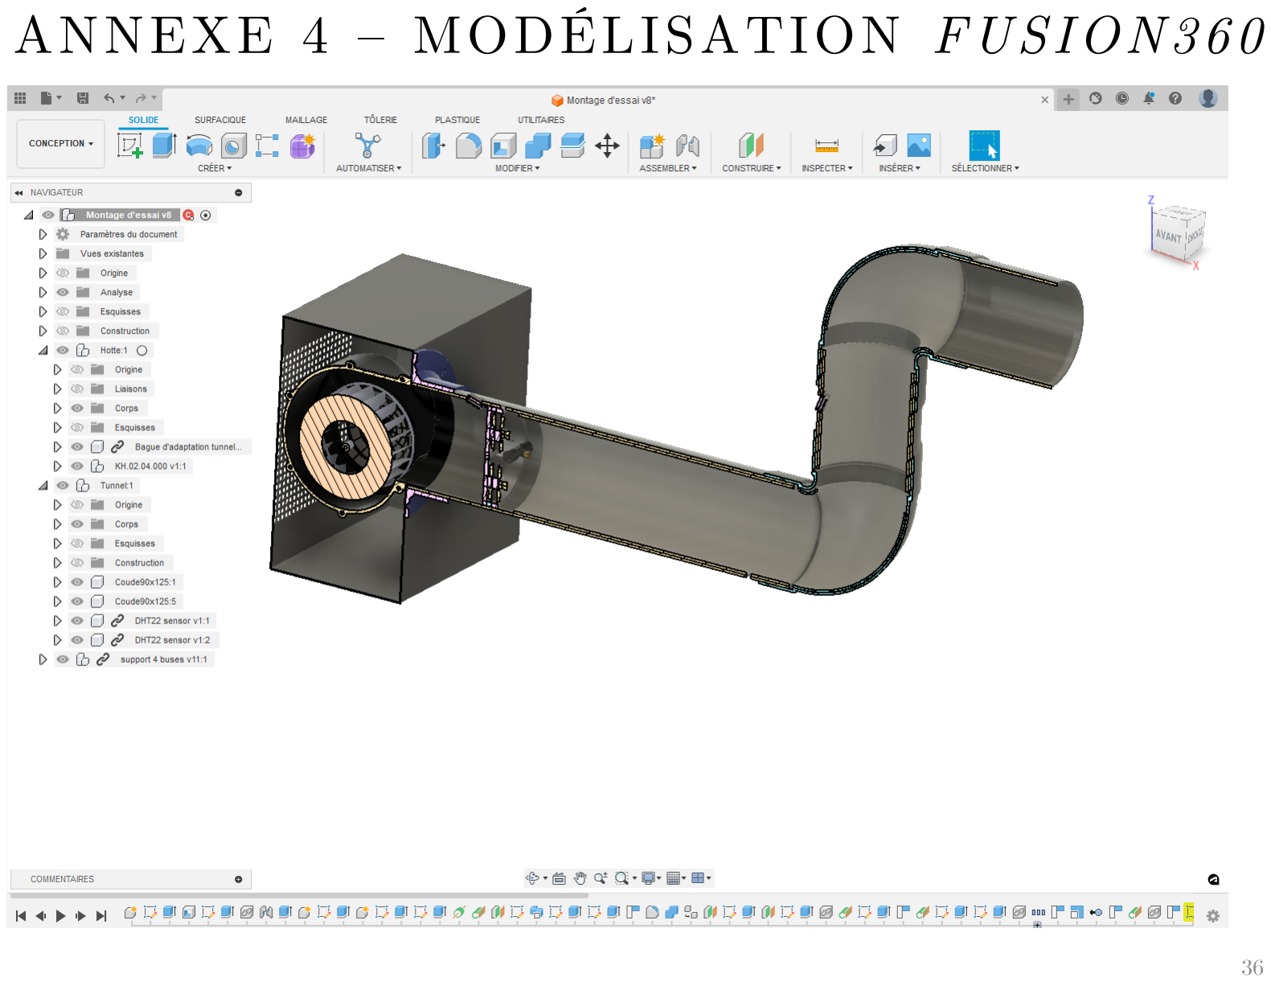
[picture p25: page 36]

Emilien WOLFF 2022-2023 | 37

# ANNEXE 5 – CODE SOURCE POUR L’ARDUINO DE CONTROLE

/*
TIPE Air Conditioner based on water phase change

Version 1.0

The circuit:
* LCD RS pin to digital pin 7
* LCD Enable pin to digital pin 6 * LCD D4 pin to digital pin 5
* LCD D5 pin to digital pin 4
* LCD D6 pin to digital pin 3
* LCD D7 pin to digital pin 2 * LCD R/W pin to ground
* LCD VSS pin to ground
* LCD VCC pin to 5V
* wiper to LCD VO pin (pin 3) * DHT1 DATA pin 8
* DHT2 DATA pin 9
* BUTTON pin 11
* ELECTROVANNE pin 12
* BACKLIGHT on/off pin 13

Pour ARDUINO UNO
*/
#include <EEPROM.h>

#include <LiquidCrystal.h> #include <Stepper.h>

#include "DHT.h"

#include <AutoPID.h>

//#define DEBUG_TRACE | // debug with main informations
//#define DEBUG_VERBOSE | // more about details
//#define DEBUG_SIMUL | // If no sensor connected, do random values to test the code
#define DEBUG_CONSOLE | // During the measurement, display the values on the console at a different pace than

on the EEPROM
#define TRUE 1

Emilien WOLFF 2022-2023 | 38

#define FALSE 0

#define ON 1

#define OFF 0

#define MAX_QTITE 9 | // maximum value for the "reglage" which is the index of water quantity. Over that, not

take into account
#define MAX_LCD_LINE 16

#define BACKLIGHT_ON LOW

#define BACKLIGHT_OFF HIGH

#define DEBOUNCE 50

#define T_INJECTION_UNITAIRE 200 // in ms

#define T_ATTENTE_INJECTION 30000 // in ms, unitary duration between two injections

#define T_MESURE 2500 // in ms time between two measurement read on DHT22 (supports 2sec minimum) #define T_RAFRAICHISSEMENT_LCD 500

#define T_APPUI_COURT 100

#define T_APPUI_LONG | 3000 | // Duration to qualify a long press

#define T_APPUI_TRES_LONG 6000

#define T_APPUI_SUPER_LONG 9000

#define NB_MESURES_AVANT_STOCKAGE 12 | // every N measurement, the values are stored in EEPROM

#define NB_MESURES_AVANT_PRINT_CONSOLE 2 | // every N measurement, the values are printed on the console

#define T_SECONDE 1000 | // One second

#define PAUSE_MEMO_DELAY 4000 | // delay after which the value is stored in EEPROM. Should be less than led_delay

#define PAUSE_LED_DELAY | 10000 // delay after which the backlight is swithed OFF

#define PAUSE_BLINK_ON 500

#define PAUSE_BLINK_OFF 500

#define BUTTON_PRESSED LOW

#define BUTTON_RELEASED HIGH

#define VANNE_ON LOW

#define VANNE_OFF HIGH

#define DHTTYPE DHT22 | // DHT 22 | (AM2302), AM2321

#define COMMA 44 | // the comma in ascii

#define CR | 13 | // carriage return

#define LF | 10 | // Line feed

#define EEPROM_START_OFFSET 1 | // the BYTE 0 is used to store the water quantity index "reglage"

////////////////
// PARAMETERS
////////////////
//#define COMP_OFFSET | // comment if the offset compensation must be disabled
#define ZERO_OFFSET_TEMPERATURE 15.5 | // temperature at which the two sensors show the same value

#define OFFSET_TEMPERATURE | 36.7 | // wrong temperature where the offset is defined

#define OFFSET_VALUE 1.7 | // ofset True value - Bad value

// formule: Treel = Tmes + ( OFFSET_VALUE / (OFFSET_TEMPERATURE-ZERO_OFFSET_TEMPERATURE) ) * ( Tmes-ZERO_OFFSET_TEMPERATURE)

/////////////////////////
// ASSIGNATIONS OF PINS

Emilien WOLFF 2022-2023 | 39

/////////////////////////
#define LCD_RS_PIN 7

#define LCD_EN_PIN 6

#define LCD_D4_PIN 5

#define LCD_D5_PIN 4

#define LCD_D6_PIN 3

#define LCD_D7_PIN 2

#define DHT1_PIN 8 | // Digital pin connected to the DHT sensor

#define DHT2_PIN 9 | // Digital pin connected to the DHT sensor

#define DHT3_PIN 10 | // Digital pin connected to the DHT sensor

#define BUTTON_PIN 11 | // For Menu and value change

#define VANNE_PIN 12 | // for water inflow

#define BACKLIGHT_PIN 13

// initialize the sensor lib
// Connect pin 1 (on the left) of the sensor to +5V
// NOTE: If using a board with 3.3V logic like an Arduino Due connect pin 1
// to 3.3V instead of 5V!
// Connect pin 2 of the sensor to whatever your DHTPIN is
// Connect pin 3 (on the right) of the sensor to GROUND (if your sensor has 3 pins)
// Connect pin 4 (on the right) of the sensor to GROUND and leave the pin 3 EMPTY (if your sensor has 4 pins) DHT dht1(DHT1_PIN, DHTTYPE);
DHT dht2(DHT2_PIN, DHTTYPE);
// DHT dht3(DHT3_PIN, DHTTYPE);
// The process has long time characteristics (TAU= 8 minutes). No need to update too fast for PID // Code source for PID: https://reference.arduino.cc/reference/en/libraries/autopid/

#define PID_UPDATE_DELAY 10000 // regulation recalculation interval.

//pid settings and gains
#define OUTPUT_MIN 0

#define OUTPUT_MAX 255

#define KP 5

#define KI .01

#define KD 0

#define REGLAGE_INJECTION_MIN 0 | // Minimum water injection units of unitary time

#define REGLAGE_INJECTION_MAX 8 | // Maximum value corresponding to the exchange surface to avoid flood

#define MANUAL 0

#define AUTO 1

#define TARGET_OUTPUT_TEMP 25 | // So far fixed value for tests.

double t1,t2,h1,h2,setPoint,outputVal;

//input/output variables passed by reference, so they are updated automatically

Emilien WOLFF 2022-2023 | 40

AutoPID myPID(&t1, &setPoint, &outputVal, OUTPUT_MIN, OUTPUT_MAX, KP, KI, KD); unsigned long lastTempUpdate; //tracks clock time of last temp update

// initialize the library by associating any needed LCD interface pin
// with the arduino pin number it is connected to
// Code source for LCD: https://docs.arduino.cc/learn/electronics/lcd-displays

LiquidCrystal lcd(LCD_RS_PIN, LCD_EN_PIN, LCD_D4_PIN, LCD_D5_PIN, LCD_D6_PIN, LCD_D7_PIN);

////////////
// VARIABLES
////////////
int reglage = 0; | // Default value of water quantity is NONE
int duree_injection = 0;
char niveau_precedent_inc = BUTTON_RELEASED; | // to detect a edge of button press
unsigned long temps_aff = 0; | // Time reference from which the different functions estimate the passed time
to trigger the execution
unsigned long temps_mesure = 0; | // Measurement
unsigned long temps_memo = 0; | // "reglage" value stored in EEPROM
unsigned long temps_distri = 0; | // water injection
unsigned long temps_blink = 0; | // blink pace of black square
unsigned long temps_appui_long = 0; | // long press
unsigned long temps_aff_lcd = 0; | // LCD value writing to avoid massive writes in the main loop
enum t_appui {AUCUN,COURT,LONG,TRES_LONG,SUPER_LONG}; | // Button press types
t_appui type_appui = AUCUN;
unsigned long decompte = T_ATTENTE_INJECTION; // countdown between injection
char blink_state = ON;
char afficheur_eteint=TRUE;
char vanne_ouverte = FALSE;
char valeur_memorisee = TRUE; char valeur_affichee = FALSE; char injection_eau = FALSE ; byte probleme_capteurs = FALSE;
byte go_record = FALSE;
byte regulation_mode = MANUAL;
int eeprom_current_address = EEPROM_START_OFFSET ; int nb_mesures = 0;
byte nb_mesures_stockees = 0;

//////////////
// FUNCTIONS
//////////////

void Display_valeur(int valeur){

Emilien WOLFF 2022-2023 | 41

//debug=valeur;
if (valeur > MAX_QTITE) valeur=0; | // if out of allowed values range, display a 0 (abnormal)
digitalWrite(BACKLIGHT_PIN,BACKLIGHT_ON); | // switch backlight LCD on
lcd.setCursor(10,1);
lcd.print(valeur);
afficheur_eteint = FALSE;
valeur_affichee = TRUE;
// new time reference for the backlight temps_aff = millis();
#if defined(DEBUG_TRACE)

Serial.print("Display: "); Serial.println(valeur);
#endif

}

void Display_sensors(float HRin, float Tin, float HRout, float Tout) {
String FirstLineString = ""; digitalWrite(BACKLIGHT_PIN,BACKLIGHT_ON);
// new time reference for the backlight
temps_aff = millis();
// Reading temperature or humidity takes about 250 milliseconds!
// Sensor readings may also be up to 2 seconds 'old' (its a very slow sensor) if (isnan(HRin) || isnan(Tin) || isnan(HRout) || isnan(Tout))
{
FirstLineString+="Err capteurs";
#if defined(DEBUG_TRACE)

Serial.println(F("Failed to read from DHT sensors!")); #endif
}
else
{
FirstLineString+=String(int(HRin))+ "%" + String(Tin,1)+ " " + String(int(HRout))+ "%" + String(Tout,1) ; }
lcd.setCursor(0,0);
lcd.print(FirstLineString);
afficheur_eteint = FALSE;
#if defined(DEBUG_VERBOSE) Serial.print("FirstLineString: "); Serial.println(FirstLineString); #endif

}

void Display_message(String msg, byte x, byte y) {

Emilien WOLFF 2022-2023 | 42
if ((msg.length()> MAX_LCD_LINE-x) || (y>1) ) msg="ERREUR"; | // the string is too long or out of the screen
coordinates
// if the string may overwrite the water injection value, go to second line
if ( ((msg.length()+x) > 9) && (y==1) ) valeur_affichee = FALSE; digitalWrite(BACKLIGHT_PIN,BACKLIGHT_ON);
//lcd.clear();
lcd.setCursor(x,y);
lcd.print(msg);
afficheur_eteint = FALSE;
temps_aff = millis();
}

void Display_square(char state){ //debug=state;
lcd.setCursor(11,1);
if (state == ON) lcd.print((char)255); if (state == OFF) lcd.print(" ");
}

void Display_countdown(void)
{
int tmp=0;
tmp=(T_ATTENTE_INJECTION-(millis()-temps_distri))/1000; lcd.setCursor(14,1);
if(tmp>9)
{
lcd.print(tmp);
}
else
{
lcd.print(" ");
lcd.print(tmp);
}
}

void Eeprom_to_console(void)
{
int addr = EEPROM_START_OFFSET;
int i=0;
Serial.println(F("Programme " __FILE__ " le " __DATE__ "\r\n")); Serial.print("Instants espacés de (s): "); Serial.println(String(NB_MESURES_AVANT_STOCKAGE*T_MESURE/1000)); Serial.println("Mesures: ");
Serial.println("Instant %HRin Tin %HRout Tout");

Emilien WOLFF 2022-2023 | 43

#if defined(DEBUG_VERBOSE)

Serial.println("addr=" + String(addr) + " Length=" + String(EEPROM.length())); for(i=0;i<26;i++)
{
Serial.print(EEPROM.read(addr+i));
Serial.print(",");
}
Serial.println("");
i=0;
#endif

while ((EEPROM.read(addr)!=0) && (addr < EEPROM.length()))
{ | // after each group of values, there may be an end of record NULL
if(i==5)
{ | // end of the bloc of 5 BYTES
Serial.println(""); | // next line printed
i=0;
}
if (i==2 || i==4)
{ // position 2 and 4: temperature coded one one byte multiplied by 5 for less precision loss Serial.print(String(EEPROM.read(addr)/5.0,1));
}
else
{ // other values written with no change Serial.print(String(EEPROM.read(addr))); }
Serial.print(",");
addr++;
i++;
delay(20);
}
Serial.println("");
}

void Values_to_eeprom(byte instant, float HRin, float Tin, float HRout, float Tout) {
byte hr1, temp1, hr2, temp2;
// encoding the FLOAT into ONE BYTE
hr1=(byte)(int)(HRin+.5); // round to the near integer value, then cast to one BYTE temp1=(byte)(int)(Tin+.5);
hr2=(byte)(int)(HRout+.5);
temp2=(byte)(int)(Tout+.5);
if( (eeprom_current_address + 5) < EEPROM.length()) { // there are still places for one set of data EEPROM.update(eeprom_current_address, instant); eeprom_current_address++;

Emilien WOLFF 2022-2023 | 44

EEPROM.update(eeprom_current_address, hr1); eeprom_current_address++;
EEPROM.update(eeprom_current_address, temp1); eeprom_current_address++;
EEPROM.update(eeprom_current_address, hr2); eeprom_current_address++;
EEPROM.update(eeprom_current_address, temp2); eeprom_current_address++;
#if defined(DEBUG_VERBOSE)

Serial.println("Next addr=" + String(eeprom_current_address)); #endif
}
else
{ // stop needed
#if defined(DEBUG_TRACE)

Serial.println(F("EEPROM pleine. On arrete...")); #endif
if(eeprom_current_address = EEPROM.length())
{ // no more storage available
EEPROM.update(eeprom_current_address-1, 0); // overwrite the last measurement to end the record with NULL
}
else
{ // still one place free
EEPROM.update(eeprom_current_address, 0); // ending the record with NULL }
go_record = FALSE; // and we stop writing to the EEPROM Display_message("Stop Enreg",0,1);
nb_mesures=0;
}
}

void check_button(void)
{
// When the button is pressed, LCD backlight is switched ON and the current "reglage" is displayed
// To increment the reglage, a second press is needed. As long as the button is pressed, skip this test // Next press with LCD ON does increment the value, and reaching MAX_QTITE loops to 0
// LONG press on the button shows successively other options (Menu)

// ACTION WHEN THE BUTTON IS PRESSED

if((niveau_precedent_inc == BUTTON_RELEASED) && digitalRead(BUTTON_PIN) == BUTTON_PRESSED )
{ | // button now pressed
delay(DEBOUNCE); | // waiting some short ms to confirm the button is still in same state, to avoid a bounce
if(digitalRead(BUTTON_PIN) == BUTTON_PRESSED)

Emilien WOLFF 2022-2023 | 45

{
temps_appui_long=millis(); // réference de temps pour qualifier l'appui long niveau_precedent_inc = BUTTON_PRESSED;
#if defined(DEBUG_TRACE)

Serial.println("appui");
#endif

}
}

// ACTIONS ASSOCIATED TO THE BUTTON RELEASE TIME (AFTER LONG PRESS)

if((niveau_precedent_inc == BUTTON_PRESSED) && digitalRead(BUTTON_PIN) == BUTTON_RELEASED )
{ | // button now released
delay(DEBOUNCE); | // waiting some short ms to confirm the button is still in same state, to avoid a bounce
if(digitalRead(BUTTON_PIN) == BUTTON_RELEASED)
{ // confirmed ! Now we qualify the press type based on passed time
niveau_precedent_inc = BUTTON_RELEASED;
#if defined(DEBUG_TRACE)

Serial.print("lache (ms): "); Serial.println(String(millis()-temps_appui_long)); #endif
if((millis()-temps_appui_long) > T_APPUI_SUPER_LONG) {
type_appui = SUPER_LONG;
#if defined(DEBUG_TRACE)

Serial.println("appui SUPER long"); #endif
}
else
{
if((millis()-temps_appui_long) > T_APPUI_TRES_LONG) {
type_appui = TRES_LONG;
#if defined(DEBUG_TRACE)

Serial.println("appui TRES long"); #endif
}
else
{
if((millis()-temps_appui_long) > T_APPUI_LONG) {
type_appui = LONG;
#if defined(DEBUG_TRACE)

Serial.println("appui long"); #endif

Emilien WOLFF 2022-2023 | 46

}
else
{
if((millis()-temps_appui_long) > T_APPUI_COURT) {
type_appui = COURT;
#if defined(DEBUG_TRACE)

Serial.println("appui court"); #endif
}
}
}
}
}
}

// MENU PRESENTATION DEPENDING ON BUTTON PRESS TIME

if((niveau_precedent_inc == BUTTON_PRESSED) && digitalRead(BUTTON_PIN) == BUTTON_PRESSED )
{ // The button is still pressed: display successively the menu options which will be validated at button release
if(millis()-temps_appui_long> T_APPUI_SUPER_LONG)
{ // SUPER LONG press time passed => Mode toggle if( millis()-temps_aff_lcd > T_RAFRAICHISSEMENT_LCD) {
Display_message("Mode | ",0,1);
temps_aff_lcd=millis();
#if defined(DEBUG_TRACE)

Serial.println("Mode");
#endif

}
}
else
{
if(millis()-temps_appui_long> T_APPUI_TRES_LONG)
{ // VERY LONG press time passed => Console
if( millis()-temps_aff_lcd > T_RAFRAICHISSEMENT_LCD) {
Display_message("Console Print",0,1); temps_aff_lcd=millis();
#if defined(DEBUG_TRACE)

Serial.println("Console Print"); #endif
}
}

Emilien WOLFF 2022-2023 | 47

else
{ // c'est peut -être un appui long seulement if(millis()-temps_appui_long> T_APPUI_LONG) { // LONG press time passed => Recording if(go_record==TRUE)
{
if( millis()-temps_aff_lcd > T_RAFRAICHISSEMENT_LCD) {
Display_message("Stop Enreg ",0,1); temps_aff_lcd=millis();
#if defined(DEBUG_TRACE)

Serial.println("Stop Enreg"); #endif
}
}
else
{
if( millis()-temps_aff_lcd > T_RAFRAICHISSEMENT_LCD) {
Display_message("Go Enreg...",0,1); temps_aff_lcd=millis();
#if defined(DEBUG_TRACE)

Serial.println("Go Enreg..."); #endif
}
}
}
else
{
if(millis()-temps_appui_long> T_APPUI_COURT+T_RAFRAICHISSEMENT_LCD) { // Short press time passed => Quantity
if( millis()-temps_aff_lcd > T_RAFRAICHISSEMENT_LCD)
{
Display_message("Quantite ",0,1); temps_aff_lcd=millis();
#if defined(DEBUG_TRACE)

Serial.println("Quantite"); #endif
}
}
}
}
}
}
}

Emilien WOLFF 2022-2023 | 48

void manage_quantity_input(void)
{
// A square is blinking during the time the changed value is not stored yet in EEPROM.
if ((valeur_memorisee == FALSE) && (blink_state == ON) && (millis()-temps_blink > PAUSE_BLINK_ON)) {
Display_square(OFF);
temps_blink=millis();
blink_state = OFF;
#if defined(DEBUG_VERBOSE) Serial.println("Blink OFF"); #endif

}
if ((valeur_memorisee == FALSE) && (blink_state == OFF) && (millis()-temps_blink > PAUSE_BLINK_OFF)) {
Display_square(ON);
temps_blink=millis();
blink_state = ON;
#if defined(DEBUG_VERBOSE) Serial.println("Blink ON"); #endif

}
// LCD backlight is switched OFF after a delay after last press
if ((afficheur_eteint == FALSE) && (millis()-temps_aff > PAUSE_LED_DELAY)) {
digitalWrite(BACKLIGHT_PIN,BACKLIGHT_OFF);
afficheur_eteint = TRUE;
#if defined(DEBUG_VERBOSE) Serial.println("Extinction affichage"); #endif

}
// Storage of the value after a given delay following the last change
if ((valeur_memorisee == FALSE) && (millis()-temps_memo > PAUSE_MEMO_DELAY) ) {
if (EEPROM.read(0) != reglage)
{
EEPROM.write(0, reglage); // update of the chosen value in EEPROM if changed }
valeur_memorisee = TRUE;
#if defined(DEBUG_TRACE)

Serial.println("Memorisation valeur"); #endif
Display_square(OFF);
afficheur_eteint = FALSE;
}

Emilien WOLFF 2022-2023 | 49

}

void manage_injection(void)
{
if(millis()-temps_distri < T_INJECTION_UNITAIRE*reglage) { // start of injection
if(vanne_ouverte==FALSE)
{
digitalWrite(VANNE_PIN,VANNE_ON); vanne_ouverte=TRUE;
#if defined(DEBUG_TRACE)

Serial.println("Ouverture vanne"); #endif
}
}
else
{ // injection duration is passed digitalWrite(VANNE_PIN,VANNE_OFF);
injection_eau = FALSE; // work is done
vanne_ouverte = FALSE;
temps_distri = millis(); // New time reference for the next distribution instant. #if defined(DEBUG_TRACE)
Serial.println("fin distri");
Serial.println("");
#endif

}
}

void manage_display(void)
{
t1 = dht1.readTemperature(); t2 = dht2.readTemperature(); h1 = dht1.readHumidity();
h2 = dht2.readHumidity();

if (isnan(h1) || isnan(t1) || isnan(h2) || isnan(t2)) {
Display_message("Err capteurs", 0, 0);
probleme_capteurs = TRUE;
#if defined(DEBUG_TRACE)

Serial.println(F("Erreur lecture des capteurs DHT!")); #endif

Emilien WOLFF 2022-2023 | 50

}
else
{
probleme_capteurs = FALSE;
Display_sensors(h1, t1, h2, t2);
#if defined(DEBUG_VERBOSE)

Serial.println("nbmes" + String(nb_mesures) +" reste " + String(nb_mesures % NB_MESURES_AVANT_STOCKAGE) + " Go_Rec " + String(go_record) + " PB Capteur" + String(probleme_capteurs)); #endif
if( (probleme_capteurs==FALSE) && (go_record == TRUE) && ((nb_mesures % NB_MESURES_AVANT_STOCKAGE) == 0))
{ | // | Store one over N values
nb_mesures_stockees++;
Values_to_eeprom(nb_mesures_stockees, h1, (t1*5.0), h2, (t2*5.0));
// store in a BYTE (on 255) a value with a comma: 25.3 => 253 / 2 => 126 }
}
nb_mesures++;
}
}

///////////////////
// INITIALISATION
///////////////////

// the setup routine runs once when you press reset: void setup() {
// make the pushbutton's pin an input: pinMode(BUTTON_PIN,INPUT_PULLUP);
// LCD backlight
pinMode(BACKLIGHT_PIN,OUTPUT); digitalWrite(BACKLIGHT_PIN,BACKLIGHT_OFF); // water injection
pinMode(VANNE_PIN,OUTPUT); digitalWrite(VANNE_PIN,VANNE_OFF);
// set up the LCD's number of columns and rows: lcd.begin(16, 2);
// the two temp & HR sensors
dht1.begin();
dht2.begin();

// if temperature is more than 4 degrees below or above setpoint, OUTPUT will be set to min or max respectively
myPID.setBangBang(4);

Emilien WOLFF 2022-2023 | 51

//set PID update interval
myPID.setTimeStep(PID_UPDATE_DELAY);

setPoint = TARGET_OUTPUT_TEMP; // For the tests, set the target to a fixed value. Do a menu else.

Serial.begin(9600);
// Read the previous setting value from EEPROM
reglage = EEPROM.read(0); // the manual setting of water injection is stored in address 0. #if defined(DEBUG_TRACE)
Serial.println("Init faite"); #endif
temps_mesure=millis();
temps_distri=millis();
decompte=millis()-temps_distri; valeur_affichee=FALSE;
type_appui=AUCUN;
lcd.clear();
Display_message("Quantite: ",0,1);
Display_valeur(reglage);
Display_countdown();
eeprom_current_address = EEPROM_START_OFFSET ; // The available storage pointer starts after the storage of the internal constants.

}

////////////////////////
// MAIN LOOP FOREVER ///
////////////////////////

void loop() {

check_button(); // sets the "type_appui" depending on the user action

// Setup several state values based on the press type switch(type_appui)
{
case AUCUN:
break;
case COURT: // Backlight ON and display current state OR increase the quantity of water if press again if (afficheur_eteint == TRUE || valeur_affichee==FALSE)
{ // immediate action: display switched ON with current value displayed Display_message("Quantite: ",0,1);
Display_valeur(reglage);

Emilien WOLFF 2022-2023 | 52

#if defined(DEBUG_TRACE)

Serial.println("Bouton Appuye"); #endif
afficheur_eteint = FALSE;
valeur_affichee = TRUE;
}
else
{
reglage+= 1;
#if defined(DEBUG_TRACE)

Serial.println("Bouton Réappuyé");
#endif

valeur_memorisee = FALSE; // The value just changed, now need to store after a delay less than LCD swich-on time temps_aff = millis(); // reference of time for the LCD OFF
temps_memo = millis(); // reference of time for the setting being stored
if (reglage > MAX_QTITE) reglage=0;
Display_valeur(reglage);
delay(200);
}
type_appui = AUCUN; // processing finised, reset button state. break;
case LONG: | // start/stop of the recording
if(go_record==TRUE)
{ // STOPPE
go_record = FALSE;
// still need to finish the record with the NULL character if(eeprom_current_address == EEPROM.length())
{ // eeprom_current_address points on the next storage address, if equal to EEPROM size, no more space
EEPROM.update(eeprom_current_address-1, 0); // Overwrite the last value with the NULL character (end of record) #if defined(DEBUG_VERBOSE)
Serial.println("NULL ecrit en(-1):" + String(eeprom_current_address-1)); #endif
}
else
{ // there is still one place left EEPROM.update(eeprom_current_address, 0);
eeprom_current_address++;
#if defined(DEBUG_VERBOSE)

Serial.println("NULL ecrit en:" + String(eeprom_current_address)); #endif
}
Display_message("Fin Enrg OK",0,1);

Emilien WOLFF 2022-2023 | 53

nb_mesures=0;
nb_mesures_stockees=0;
// We could restart next record from here. In this case, comment this next instruction
eeprom_current_address=EEPROM_START_OFFSET;
delay(1000);
type_appui = COURT; // Processing finished, trigger the quantity display by setting the relevant keypress type }
else
{ // LET'S START
go_record = TRUE;
nb_mesures=0; | // start of the measurement counter
// We could restart next record from here. In this case, comment this next instruction
nb_mesures_stockees=0;
Display_message("Enrg actif",0,1);
type_appui = AUCUN; // processing finised, reset button state.. }
break;
case TRES_LONG: // Print the data from EEPROM to the console (USB) Eeprom_to_console();
Display_message("Aff Termine ",0,1);
delay(1000);
type_appui = COURT; // Processing finished, trigger the quantity display by setting the relevant keypress type
break;
case SUPER_LONG: // Switch between AUTO and MANUAL if(regulation_mode == AUTO)
{
Display_message("Manuel | ",0,1);
delay(1000); | // needed to ensure readability. Rare exception of delay() use.
regulation_mode = MANUAL;
reglage = EEPROM.read(0); // reload the manual value from memory type_appui = COURT;
}
else
{
Display_message("Automatique ",0,1); delay(1000);
regulation_mode = AUTO;
type_appui = COURT;
}
break;
default:

Emilien WOLFF 2022-2023 | 54

#if defined(DEBUG_TRACE)

Serial.println("switch default"); #endif
break;
}

manage_quantity_input(); // simple press of the button does increase the quantity of water to inject. // Does also store this value in EEPROM and display it.

// As soon as the injection period is passed, the distribution is triggered
// Principle: opening of the valve is a multiple named "reglage" of a fixed value T_INJECTION_UNITAIRE // and the time between two injections is set by T_ATTENTE_INJECTION.
// If reglage = 0, no injection => deactivated.

if( (millis()-temps_distri) > T_ATTENTE_INJECTION )
{
#if defined(DEBUG_TRACE)

Serial.println("Faut distribuer!");
#endif

// Here the water injection is done
// define the "reglage" value between REGLAGE_INJECTION_MIN and REGLAGE_INJECTION_MAX // to correspond to PID 0 and 255
if(regulation_mode == AUTO)
{ // take the PID output value as reglage instead of the manual one.
reglage = (uint8_t)(outputVal*REGLAGE_INJECTION_MAX/255 + REGLAGE_INJECTION_MIN); }
manage_injection(); // Does open the water valve the right duration
// The reference time is set in this function once the injection is done
}

// Display the temperature and humidity values periodically at T_MESURE if(millis()-temps_mesure > T_MESURE)
{
manage_display(); // Display values
temps_mesure=millis();
}

// Update the countdown value every second
if( (millis()-decompte) > T_SECONDE)
{ | // more than 1 second passed
Display_countdown(); | // count down between two injections
decompte=millis();
}

//call every loop, updates automatically at certain time interval

Emilien WOLFF 2022-2023 | 55
if(regulation_mode == AUTO) | myPID.run();

}

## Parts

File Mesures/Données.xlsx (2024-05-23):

Description | Paramètres d'étude | Valeur | Unité | Résultats | Valeur | Unité
Température de la pièce voulue | Tobj | 25 | °C | Puissance de la clim | 1.76 | kW
Humidité relative intérieure | HR% int |  |  | Débit de l'eau | 2.8 | l/h
Température extérieure | Text | 35 | °C | Débit de l'air | 433.8094078 | m3/h
Humidité relative extérieure | HR% ext
Surface au sol | Ssol | 20 | m²
Hauteur sous plafond | h | 2.5 | m
Nombre de fenêtres dans la pièce | Nfen | 1 | fenètres
Masse volumique de l'eau | reau | 997 | kg/m3
Variation d'humidité absolue | DHA | 5 | gH20/kgair
Chaleur latente de l'eau | Dhce | 2257 | kJ/kg
Masse volumique de l'air | rair | 1.292 | kg/m3

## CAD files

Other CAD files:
Modélisation-3D/Pièce climaitsée.f3d
Modélisation-3D/Support 4 buses.f3d
Modélisation-3D/Support une buse.f3d
